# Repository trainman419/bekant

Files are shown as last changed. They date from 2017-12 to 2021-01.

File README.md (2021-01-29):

# IKEA Bekant Desk Controller

This is a simple Arduino firmware to control the IKEA Bekant motorized sit/stand desk.

## Circuit

The circuit for this sketch is based on an MCP2003B LIN transceiver.

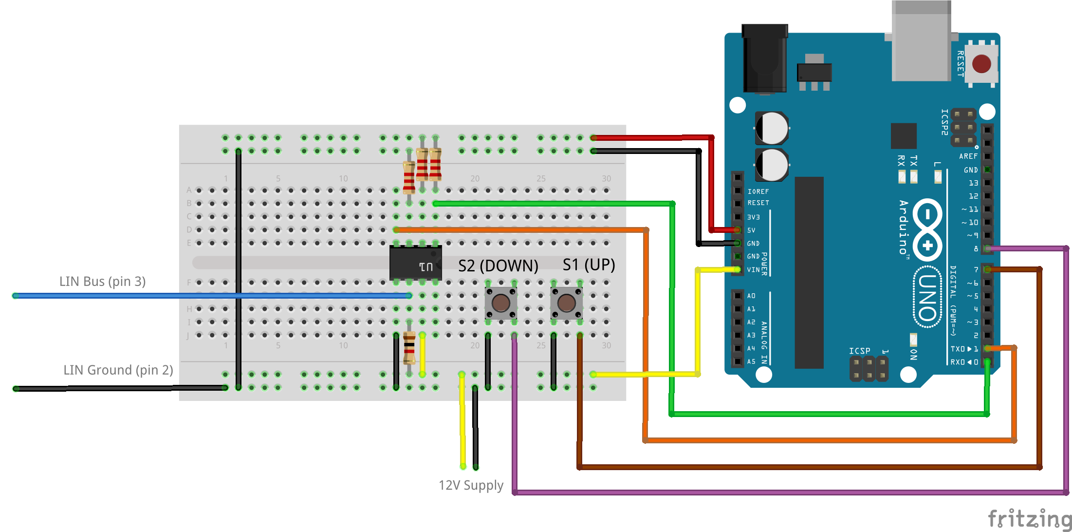
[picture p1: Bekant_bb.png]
Breadboard


And the accompanying schematic.

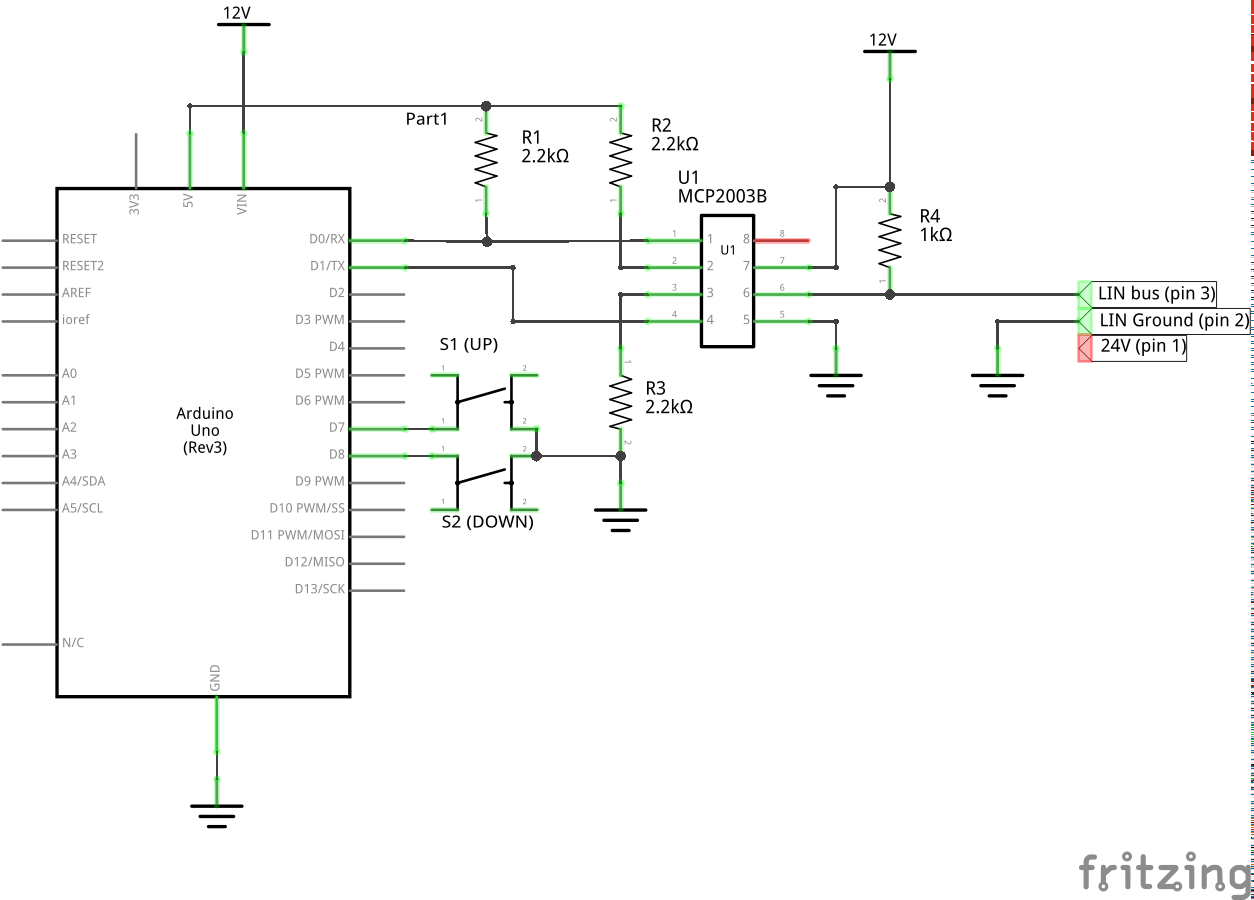
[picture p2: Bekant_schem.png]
Schematic


## Details of operation

Based on a blog post by Robert Nixdorf<sup>[1](#1)</sup>, it's quite clear that the desk is using the 1-wire LIN protocol<sup>[2](#2)</sup> to communicate between the controller and motors in both legs of the desk.

I've seen other posts from Gina Häußge<sup>[4](#4)</sup>, on the EEVblog forum <sup>[7](#7)</sup>, from Robin Reiter<sup>[6](#6)</sup>, and reposted on Hackaday<sup>[8](#8)</sup> and the AdaFruit Blog<sup>[9](#9)</sup>, but none of these have deciphered the LIN command protocol or completely replaced the existing controller. These hacks mostly focus reading the encoder value from LIN and sending button presses to the controller board, but modifications are a little messy, and I'd rather just plug into the bus and send commands directly.

LIN is a single-master bus, so in order to send commands we need to unplug the controller completely and replicate everything that it was doing in the replacement device. Luckily the protocol is simple, so this isn't too hard.

I am lucky enough to have access to an oscillocope that can do LIN decoding, so I used that extensively during my hacking and debugging.

The bus schedule was obvious by looking at the traffic. There is sequence of 10 messages, spaced 5 ms apart that repeat every 200ms. The ID sequence is 0x11, 0x08, 0x09, 0x10, 0x10, 0x10, 0x10, 0x10, 0x10, 0x01, 0x12.

I implemented a simple LIN master with an Arduino and a MCP2003B LIN transciever based on Andrew Stone's LIN library for arduino<sup>[5](#5)</sup> that can send these commands in the correct sequence, with the correct timing.

LIN is a single-wire shared bus, so it's impossible to tell which node is transmitting from a packet trace or oscilloscope readout. I know that the master must transmit the ID, so I set up my LIN master to transmit the IDs in sequence with no data. I saw that another device (presumably the motors) responded to IDs 0x08 and 0x09, so I know that the master should be reading from those IDs, and writing to the other IDs.

This means that the protocol is:

```
0x11: TX 0, 0, 0
0x08: RX 3 bytes
0x09: RX 3 bytes
0x10: TX 0 bytes; repeat 6 times
0x01: TX 0 bytes
0x12: TX 3 bytes
```

From my own decoding, and confirmed by the packet dumps in Robert Nixdorf's github repo<sup>[3](#3)</sup>, the pack format for 0x08, 0x09 and 0x12 seems to be a two-byte encoder value followed by a status or command byte. The first byte of the encoder value increments more quickly when the table is moving, so this is probably the LSB.

I've only seen three status codes on ID's 0x08 and 0x09:
```
0x60 desk not moving
0x02 starting to move
0x03 moving
```

I've seen more commands in the 0x12 message. These seem to be sent in a specific sequence:
```
0xFC not moving
0xC4 sent immediately before moving
0x86 up
0x85 down
0x87 1st command before stopping
0x84 2nd command before stopping
```

There are several other command codes in Robert Nixdorf's packet dumps that I haven't decoded yet. It looks like they are probably related to movement of the desk near the upper and lower limits.

I don't competely understand how the encoder values are used yet. Here are my observations so far:
 * The encoder values are clearly encoder values; they increment and the upper byte increments or decrements when the lower byte rolls over.
 * Higher values correspond to higher desk positions.
 * The encoder value in 0x08 always seems to be higher than 0x09. Unclear if this is by design or coincidence.
 * The encoder value in 0x12 seems to be a copy of the value in 0x08 or 0x09 most of the time, but I have occasionally seen other values.

I _think_ the encoder value is a target encoder value for one or both legs, and the command byte somehow releases a brake in each leg and commands it to move.

Sending 0x87 for a prolonged period of time causes the encoder values in 0x08 and 0x09 to reach the same values. Maybe this is an absolute positioning command?

Sending the wrong encoder values with the 0x85 (down?) command causes the motors to move unevenly and the desk to tilt. Sending 0x86 followed by 0x87 eventually corrects this.

# References
 1. <a name="1">https://web.archive.org/web/20190116092248/https://blog.rnix.de/hacking-ikea-bekant/</a>
 2. <a name="2">https://en.wikipedia.org/wiki/Local_Interconnect_Network</a>
 3. <a name="3">https://github.com/diodenschein/TableMem</a>
 4. <a name="4">https://plus.google.com/u/1/+GinaH%C3%A4u%C3%9Fge/posts/3U5k1qKdLxH?pageId=none</a>
 5. <a name="5">https://github.com/gandrewstone/LIN</a>
 6. <a name="6">https://github.com/robin7331/IKEA-Hackant</a>
 7. <a name="7">https://www.eevblog.com/forum/beginners/ikea-bekant-desk-motorised-hack/</a>
 8. <a name="8">http://hackaday.com/2017/02/10/ikea-standing-desk-goes-dumb-to-smart-with-lin-bus/</a>
 9. <a name="9">https://blog.adafruit.com/2017/03/27/smarkant-ikea-bekant-adjustable-sitstand-table-controller-reverse-engineered-controlled-with-alexa/</a>

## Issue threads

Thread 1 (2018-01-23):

delay_until

brunisgirl, 2018-01-23:
Hi,

What does the delay_until do? And why did you use "5" as argument?

Thanks

trainman419, 2018-01-23:
```
unsigned long t = 0;

void delay_until(unsigned long ms) {
  unsigned long end = t + (1000 * ms);
  unsigned long d = end - micros();

  // crazy long delay; probably negative wrap-around
  // just return
  if ( d > 1000000 ) {
    t = micros();
    return;
  }

  if (d > 15000) {
    unsigned long d2 = (d-15000)/1000;
    delay(d2);
    d = end - micros();
  }
  delayMicroseconds(d);
  t = end;
}
```

`delay_until()` and the associated global `t` is used to wait the specified amount of time since the previous call to `delay_until()`. This allows me to run the same sequence of code on a schedule, even if individual function calls take a slightly different amount of time each time.

The argument to `delay_until` is the number of milliseconds to delay (since the previous call to delay_until)

For example, if I have a function `foo()` that takes 1-2 milliseconds to execute, if I my loop is:

```
void loop() {
    foo(); // 1-2 mS
    delay(5); // 5 mS
}
```

The total loop time will be between 6 and 7 milliseconds, instead of the desired 5 milliseconds. Since I cannot predict exactly how long foo() will take, I cannot just adjust the delay.

With delay_until(), this loop always takes 5 milliseconds:

```
void loop() {
    foo(); // 1-2 mS
    delay_until(5); // wait until 5mS have passed
}
```

This is particularly important for LIN because the protocol requires that the first set of messages be sent every 5 milliseconds (5mS * 10 messages = 50 mS), and the entire set of messages repeats every 200mS, so at the end of the loop I delay for the remaining 150mS: https://github.com/trainman419/bekant/blob/f3733f8a28a3442db584cdb14d0de5f904b2de64/bekant.ino#L264-L265

Again, the important thing to note here is that if I used a normal delay() between messages or at the end of the main loop, the amount of time that it takes to handle WiFi clients would increase the loop time, and the other LIN devices would probably time out.

brunisgirl, 2018-01-23:
Thanks. OK I understand. But you talk about the protocol asking for 5 ms.
Where in LIN specification you found it? Or it is only for this particular
case?

On Jan 23, 2018 8:57 PM, "Austin" <notifications@github.com> wrote:

unsigned long t = 0;

void delay_until(unsigned long ms) {
  unsigned long end = t + (1000 * ms);
  unsigned long d = end - micros();

  // crazy long delay; probably negative wrap-around
  // just return
  if ( d > 1000000 ) {
    t = micros();
    return;
  }

  if (d > 15000) {
    unsigned long d2 = (d-15000)/1000;
    delay(d2);
    d = end - micros();
  }
  delayMicroseconds(d);
  t = end;
}

delay_until() and the associated global t is used to wait the specified
amount of time since the previous call to delay_until(). This allows me to
run the same sequence of code on a schedule, even if individual function
calls take a slightly different amount of time each time.

The argument to delay_until is the number of milliseconds to delay (since
the previous call to delay_until)

For example, if I have a function foo() that takes 1-2 milliseconds to
execute, if I my loop is:

void loop() {
    foo(); // 1-2 mS
    delay(5); // 5 mS
}

The total loop time will be between 6 and 7 milliseconds, instead of the
desired 5 milliseconds. Since I cannot predict exactly how long foo() will
take, I cannot just adjust the delay.

With delay_until(), this loop always takes 5 milliseconds:

void loop() {
    foo(); // 1-2 mS
    delay_until(5); // wait until 5mS have passed
}

This is particularly important for LIN because the protocol requires that
the first set of messages be sent every 5 milliseconds (5mS * 10 messages =
50 mS), and the entire set of messages repeats every 200mS, so at the end
of the loop I delay for the remaining 150mS: https://github.com/
trainman419/bekant/blob/f3733f8a28a3442db584cdb14d0de5
f904b2de64/bekant.ino#L264-L265

Again, the important thing to note here is that if I used a normal delay()
between messages or at the end of the main loop, the amount of time that it
takes to handle WiFi clients would increase the loop time, and the other
LIN devices would probably time out.

—
You are receiving this because you authored the thread.
Reply to this email directly, view it on GitHub
<https://github.com/trainman419/bekant/issues/1#issuecomment-359911130>,
or mute
the thread
<https://github.com/notifications/unsubscribe-auth/AVm9d9d4HBNh6KV0pDWPqdkhFE5n1UpLks5tNjmtgaJpZM4RpxEQ>
.

trainman419, 2018-01-23:
The 5mS and 200mS loop rates are for this specific application. I measured these timings with my oscilloscope when I was reverse-engineering the protocol for the desk.

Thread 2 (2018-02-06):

Won't Activate - New Firmware?

joeljacobs, 2018-02-06:
I have followed your example and schematic as perfectly as possible. Quntuple-checking every connection, but the desk never moves. I have switched back and forth to the built-in controller, and it always works, but the Arduino never does. Is it possible the firmware changed on the desk?
I am also using an MCP2003 (not 2003B.) It doesn't seem like that should make a difference, but could it? The B supports LIN 2.2, and the one I have supports up to 2.1, but I can't imagine that's an issue.
Any hints? I can't troubleshoot it the way I understand, because the serial port is in use for the LIN chip.
I tried switching (using an arduino mega) to other serial pins using the constants, but it always outputted on the usb serial when connected.
I also ensure the usb serial is disconnected before testing.
Any advice would be great.

trainman419, 2018-02-06:
If you have one, your best bet would be to hook up an oscilloscope on the LIN bus and see that there's traffic (it should look similar to normal RS-232 traffic).

Trying an Arduino Mega is also an excellent debugging idea; but in addition to changing the pins ( https://github.com/trainman419/bekant/blob/master/bekant.ino#L22-L23 ) you'll also need to change the serial port used by the LIN library: https://github.com/trainman419/bekant/blob/master/bekant.ino#L26

gcormier, 2018-03-04:
Solved the issue. @joeljacobs not sure if you are still working on this.

The schematic here is missing two key diodes. (The MCP2003B reference diagram is also wrong). The official LIN spec is where I figured it out.

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

You MUST have these two diodes in serial tapped in this manner to provide the proper voltage drop.

I think otherwise, the behaviour is erratic - we can assume @trainman419 had a fully functional setup without them. I had a half functional setup, with one motor responding and the other not. Probably depends on if other parts of the circuit induce some voltage drop.

trainman419, 2018-03-04:
I never saw any signal integrity issues without the diodes that you're mentioning, and I don't remember seeing them in the LIN bus specification. Can you provide a link to documentation about these diodes, or measurements that demonstrate why they're necessary?

I do know that there is some setup that is performed by the desk's original controller that I haven't emulated yet, and I remember trying to power my desk on without the original controller would result in only a single working motor.

Usually I power on the desk with the original controller, then unplug it and plug in my Arduino.

gcormier, 2018-03-05:
Interesting on the setup - I will have to try it out.

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

Two pages down it says the diodes are mandatory.

gcormier, 2018-03-05:
Damn, I just tried it out - indeed, does not work without initially having the IKEA controller plugged in first. Sigh. Time to figure out the initialization routine!

jeffreypriebe, 2018-04-14:
@gcormier Any luck on figuring out the initialization routine?

I presume "power desk on" is referring to plugging in the desk. That is, the following should work:
1. Plug in desk (with normal desk controller)
2. Disconnect the controller
3. Attach this controller

However, reversing steps 2 & 1 will make it fail.

gcormier, 2018-04-14:
Yes I got it going. I started a project with memory functions, PCB and functional controller.

https://github.com/gcormier/megadesk

gcormier, 2018-04-14:
Oh and looking back at this issue, the diodes might not have been the root cause as I was unaware of the initialization routine. However still good to include them.

luckydonald, 2019-12-30:
Is that starting sequence now brought back into this arduino project or only available at megadesk one?

If I read @gcormier's code correctly, that's the part of https://github.com/gcormier/megadesk/blob/39d9ab13acb1d6baa30617af4301626e288f1aac/Code/megadesk.ino#L472-L565, yes?

trainman419, 2019-12-30:
I haven't ported @gcormier 's changes back to this repository. I'd be happy to accept a pull request if someone else wants to do it.

slaesh, 2020-02-07:
i am currently working on a complete replacement..
including a display, wifi and a custom enclosure! :)
just remove the old controller, replace with the new one and keep on going! ;)

will keep you guys updated =)

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

rhannink, 2021-05-05:
Hello,
I have built a LIN controller as shown in the schematic. I only use an mcp2003 e/p instead off an MCP2003B.
I have the Bekant desk plugged in with the original controller, next I remove the original controller an plug in the Arduino controller still with the Bekant desk powered on.

The desk does not respons to and button press. I see the Arduino Led lightning up when I press a button. I have also connected a logic analyser to the RX and TX pin (0 and 1) and I see LIN protocols going by. I think I even see LIN respons to ID 0x08 and LIN respons to ID 0x09.

And idea what i might be doing wrong or how I can do further debugging?

Gr. Remco
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

trainman419, 2021-05-05:
As noted before, there's an initialization sequence for the motors that I haven't reverse-engineered or implemented, but it looks like @gcormier has. I suggest you copy that init code over into this project and give it a try: https://github.com/gcormier/megadesk/blob/39d9ab13acb1d6baa30617af4301626e288f1aac/Code/megadesk.ino#L472-L565

rhannink, 2021-05-05:
Thank for your response, but I read everywhere that starting up with the original controller and then switch to the new controller should do the trick.

I am not a (real) programmer so adding the startup code is not trivial for me, but I will give it a try.

trainman419, 2021-05-05:
You write code? That makes you a programmer.

I'll tell you a little secret. I have a very fancy title at my day job and I still look things up on google and stack overflow all the time.

I tried my controller with a new desk, maybe a year or two ago, and ran into the same problem here. Couldn't get it to sync and didn't have the tools to look into it at the time.

I don't have one of these desks handy at the moment so you're probably in a better position to fix it than I am. It looks like you've got a nice logic analyzer there. I'd probably start by trying to copy or modify @gcormier's code into the arduino setup() function here. If that doesn't help, you could use your logic analyzer to capture the power-on command sequence from the original controller and modify the code here until it produces the same power-up sequence.

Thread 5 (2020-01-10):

Get MCP2003B to work with 3.3V ESP8266?

left4taco, 2020-01-10:
@trainman419 You did a very good job! I was using two relay to simulate the button but that's just an ugly solution. It's way better to communicate to the LIN bus directly.

Btw, I'm using ESP8266 in my project. The only problem is that it's output pin has a voltage of 3.3V instead of 5V on an Arduino. I checked the datasheet of [MCP2003B](http://ww1.microchip.com/downloads/en/DeviceDoc/2000546C3.pdf) and found these about the TDX and RDX:

> RDX: It has to be at a high level (> 2.5V typical) while LBUS is recessive

Looks like 3.3V from ESP8266 pin is just fine.

> TDX: has an internal pull-up

I don't if the voltage here will be 5V or 12V, but both are higher than the max tolerant voltage of ESP8266 pin.

Do you have any thought about this problem? I mean I can use a MOSFET as a gate but that seems to be an overkill.

Thanks!

zoltanhosszu, 2020-05-18:
@left4taco were you able to solve this? I'm in the exact same situation with a NodeMCU

nschurando, 2021-01-27:
Interested as well.

trainman419, 2021-01-29:
I have an MCP2003B hooked up to a [Sparkfun Thing Dev (ESP8266)](https://www.sparkfun.com/products/13711) and I have not had trouble with it.

I seem to remember finding something about this in the MCP2003B data sheet, but I don't remember exactly where.

satrik, 2021-02-22:
@trainman419 I'm also struggling with my esp8266 (Wemos D1 Mini).

To make the debugging easier, I've switched the lin.h to SoftwareSerial and use the USB port (HardwareSerial) to get some console output. I get a proper answer for the current height (enc_a).
```
12:58:30.436 -> enc_a
12:58:30.436 -> 1503
```
I'm wondering about the output of `node_a[2]` and `node_b[2]` between the 2 `switch(state)` in the loop. Neither a button is pressed or not, it shows always:
```
12:58:30.647 -> node_a[2]
12:58:30.647 -> 37
12:58:30.647 -> node_b[2]
12:58:30.647 -> 37
```

Do you have any idea what the `37` means and what I could check/test next?

Btw. I've the bigger size bekant and according to the megadesk repo, I've changed this line `if (node_a[2] == 0x00 && node_b[2] == 0x00)`. I've also tried it with 0x60, but it does not change anything so far.

b1sp, 2021-02-22:
while reading my own comment, I think I should try this `if (node_a[2] == 0x25 && node_b[2] == 0x25)`. maybe my table reports it's idle neither as 0x00 nor as 0x60 🤔

satrik, 2021-02-22:
while reading my own answer, I think I should try `if (node_a[2] == 0x25 && node_b[2] == 0x25)` 🤔
maybe my table reports it's idle as 37 and not as 96 or 0.

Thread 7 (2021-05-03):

Compiling error for esp8266

rhannink, 2021-05-03:
Hallo,

Great project, I'd like to automate my bekent desk with your project. Compiling the code for an Arduino Uno works fine, but compiling it for esp8266 with the webserver results in:

```/Users/remco/Code/Arduino/bekant/bekant.ino: In function 'int restCallback(String)':
bekant:68:15: error: 'class aREST_UI' has no member named 'buttonCallback'
   return rest.buttonCallback(answer);
               ^
/Users/remco/Code/Arduino/bekant/bekant.ino: In function 'void setup()':
bekant:87:8: error: 'class aREST_UI' has no member named 'buttonFunction'
   rest.buttonFunction("Up", &up);
        ^
bekant:88:8: error: 'class aREST_UI' has no member named 'buttonFunction'
   rest.buttonFunction("Down", &down);
        ^
exit status 1
'class aREST_UI' has no member named 'buttonCallback'
```

I have aRest library version 2.9.1 and aREST_UI library version 1.1.1 installed.

And idea what i might do wrong?

Gr. Remco

trainman419, 2021-05-04:
Huh. I don't remember which version of aREST_UI I used for this and I can't find anything about the buttonCalback or buttonFunction in their public docs or git history.

The web UI never worked terribly well to begin with; I mostly built it to prank the other people who shared my office at work. It might be better to scrap most of the web server code and start over.

I'll keep an eye out for the original source code for those libraries and let you know if I find them.

Also take a look at the megadesk project: https://github.com/gcormier/megadesk . I think he has a more complete implementation of the LIN commands and startup sequence for this desk.

trainman419, 2021-05-04:
Ah; here we are. I completely forgot that I have modified versions of the aREST_UI and aREST libraries that I was using for this project: https://github.com/trainman419/aREST_UI and https://github.com/trainman419/aREST ( I merged my changes to aREST so you just need aREST_UI )

rhannink, 2021-05-05:
Ok thanks,

I already looked at the code of megadesk, but this is strictly for tinyAT and i am not sure if it will compile on esp8266 or esp32. My goal is to het it up and running with an ESP with MQTT so I can control it from Home Assistant and Google.

Thanks for you work, I will keep you informed on my progression.

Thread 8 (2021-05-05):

New controller not doing anything

rhannink, 2021-05-05:
Hello,
I have built a LIN controller as shown in the schematic. I only use an mcp2003 e/p instead off an MCP2003B.
I have the Bekant desk plugged in with the original controller, next I remove the original controller an plug in the Arduino controller still with the Bekant desk powered on.

The desk does not respons to and button press. I see the Arduino Led lightning up when I press a button. I have also connected a logic analyser to the RX and TX pin (0 and 1) and I see LIN protocols going by. I think I even see LIN respons to ID 0x08 and LIN respons to ID 0x09.

And idea what i might be doing wrong or how I can do further debugging?

Gr. Remco

`
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

`

trainman419, 2021-05-05:
See #2 .

Closed 2021-05-05.

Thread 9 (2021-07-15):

Can my desk use 3 legs?

petersenna, 2021-07-15:
Hi I am looking into upgrading my desk, but I need 3 legs. I am considering buying 4 legs, but use only 3 of them. Problem is I could not find out if the protocol work with only one master and two slaves, or if I can have 3 slaves as well? Thank you!

petersenna, 2021-07-15:
Err I guess I got my answer on wikipedia: `LIN is a broadcast serial network comprising 16 nodes (one master and typically up to 15 slaves)`.

So I guess it is likely to work with up to 15 legs :smile:

trainman419, 2021-07-16:
I would be cautious here. I think LIN assumes that each device has a unique address and I think the Bekant legs have some protocol extension to assign unique addresses to each leg on startup. I'm not sure if that protocol extends to assigning unique address for more than two legs.

Even if the legs support it, you will probably need to spend some time porting over the initialization code ( see #2 ) and then understand it well enough to try to extend it to 3 legs.

gritstub, 2022-08-31:
@petersenna : Did you ever solve this issue? I am trying to set up a Bekant with 3 or 4 legs.

petersenna, 2022-08-31:
> @petersenna : Did you ever solve this issue? I am trying to set up a Bekant with 3 or 4 legs.

@gritstub I went on a different direction. I kept my static table.

To stand, I use monitor arm that has enough range for sitting and standing, and I use an Medical Adjustable Overbed Bedside Table for the wireless keyboard and mouse.

Notice the long pole: https://www.digitec.ch/en/s1/product/ergotron-table-mounting-arm-table-46-monitor-mount-4656121

https://www.amazon.ca/Medical-Adjustable-Overbed-Bedside-Hospital/dp/B00QMNTMXA

Closed 2022-08-31.

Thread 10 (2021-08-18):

Where to get MCP2003B? 🤔

M4RKU5-C0D3, 2021-08-18:
Hi,

I was wondering where you got the MCP2003B from? I'd prefer a DIP8 but can't find any 🙈

Greetings
Markus

trainman419, 2021-08-18:
It looks like Microchip only makes the MCP2003B in surface-mount packages.

For my prototyping I used the MCP2003B in the SOIC-8 package, on one of Adafruit's SOIC-8 breakout boards: https://www.adafruit.com/product/1212 .

The MCP2003-E/P is an older chip but it's available in a DIP package: https://octopart.com/mcp2003-e%2Fp-microchip-18190209?r=sp . I haven't tested it, but it may work in a similar way. Depending on which variant you choose, you may need to hook up some of the secondary signals differently.

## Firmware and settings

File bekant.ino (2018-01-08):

#include "lin.h"

#ifdef ESP8266
#include <ESP8266WiFi.h>
#include <aREST.h>
#include <aREST_UI.h>

// Pin settings for Sparkfun ESP8266 Thing Dev
#define UP_BTN 0
#define DOWN_BTN 13
#define LED 5
#define LED_ON LOW
#define TX_PIN 1
#define RX_PIN 3

#else
// Standard arduino settings
#define UP_BTN 7
#define DOWN_BTN 8
#define LED 13
#define LED_ON HIGH
#define TX_PIN 1
#define RX_PIN 0
#endif

Lin lin(Serial, TX_PIN);

#ifdef ESP8266
aREST_UI rest = aREST_UI();

const char * ssid = "Linksays";

WiFiServer server(80);
#endif

int height = 0;

enum class Command {
  NONE,
  UP,
  DOWN,
};

Command user_cmd = Command::NONE;

int up(bool pushed) {
  if(pushed) {
    digitalWrite(LED, LED_ON);
    user_cmd = Command::UP;
  } else {
    digitalWrite(LED, !LED_ON);
    user_cmd = Command::NONE;
  }
}

int down(bool pushed) {
  if(pushed) {
    digitalWrite(LED, LED_ON);
    user_cmd = Command::DOWN;
  } else {
    digitalWrite(LED, !LED_ON);
    user_cmd = Command::NONE;
  }
}

#ifdef ESP8266
int restCallback(String answer) {
  return rest.buttonCallback(answer);
}
#endif

void setup() {
  // put your setup code here, to run once:
  lin.begin(19200);

  pinMode(UP_BTN, INPUT_PULLUP);
  pinMode(DOWN_BTN, INPUT_PULLUP);
  pinMode(LED, OUTPUT);
  digitalWrite(LED, !LED_ON);

#ifdef ESP8266
  rest.title("Desk");
  rest.variable("Height", &height);
  rest.label("Height");
  rest.set_name("esp8266");

  rest.buttonFunction("Up", &up);
  rest.buttonFunction("Down", &down);
  rest.function("ui_callback", &restCallback);

  WiFi.mode(WIFI_AP);

  //WiFi.softAP(ssid, password);
  WiFi.softAP(ssid);

  server.begin();
#endif
}

unsigned long t = 0;

void delay_until(unsigned long ms) {
  unsigned long end = t + (1000 * ms);
  unsigned long d = end - micros();

  // crazy long delay; probably negative wrap-around
  // just return
  if ( d > 1000000 ) {
    t = micros();
    return;
  }
  
  if (d > 15000) {
    unsigned long d2 = (d-15000)/1000;
    delay(d2);
    d = end - micros();
  }
  delayMicroseconds(d);
  t = end;
}

enum class State {
  OFF,
  STARTING,
  UP,
  DOWN,
  STOPPING1,
  STOPPING2,
};

State state = State::OFF;

void loop() {
  // put your main code here, to run repeatedly:
  uint8_t empty[] = { 0, 0, 0 };
  uint8_t node_a[4] = { 0, 0, 0, 0 };
  uint8_t node_b[4] = { 0, 0, 0, 0 };
  uint8_t cmd[3] = { 0, 0, 0 };
  uint8_t res = 0;


  // Send ID 11
  lin.send(0x11, empty, 3, 2);
  delay_until(5);

  // Recv from ID 08
  res = lin.recv(0x08, node_a, 3, 2);
  delay_until(5);

  // Recv from ID 09
  res = lin.recv(0x09, node_b, 3, 2);
  delay_until(5);

  // Send ID 10, 6 times
  for (uint8_t i = 0; i < 6; i++) {
    lin.send(0x10, 0, 0, 2);
    delay_until(5);
  }

  // Send ID 1
  lin.send(0x01, 0, 0, 2);
  delay_until(5);

  uint16_t enc_a = node_a[0] | (node_a[1] << 8);
  uint16_t enc_b = node_b[0] | (node_b[1] << 8);
  uint16_t enc_target = enc_a;
  height = enc_a;

  // Send ID 12
  switch (state) {
    case State::OFF:
      cmd[2] = 0xFC; // 0b11111100
      break;
    case State::STARTING:
      cmd[2] = 0xC4; // 0b10100100
      break;
    case State::UP:
      enc_target = min(enc_a, enc_b);
      cmd[2] = 0x86; // 0b10000110
      break;
    case State::DOWN:
      enc_target = max(enc_a, enc_b);
      cmd[2] = 0x85; // 0b10000101
      break;
    case State::STOPPING1:
      cmd[2] = 0x87; // 0b10000111
      break;
    case State::STOPPING2:
      cmd[2] = 0x84; // 0b10000100
      break;
  }
  cmd[0] = enc_target & 0xFF;
  cmd[1] = enc_target >> 8;
  lin.send(0x12, cmd, 3, 2);

  // read buttons and compute next state
#ifndef ESP8266
  if (digitalRead(UP_BTN) == 0) { // UP
    up(true);
  } else if (digitalRead(DOWN_BTN) == 0) { // DOWN
    down(true);
  } else {
    up(false);
  }
#endif

  switch (state) {
    case State::OFF:
      if (user_cmd != Command::NONE) {
        if ( node_a[2] == 0x60 && node_b[2] == 0x60) {
          state = State::STARTING;
        }
      }
      break;
    case State::STARTING:
      //if( node_a[2] == 0x02 && node_b[2] == 0x02) {
        switch(user_cmd) {
          case Command::NONE:
            state = State::OFF;
            break;
          case Command::UP:
            state = State::UP;
            break;
          case Command::DOWN:
            state = State::DOWN;
            break;
        }
      //}
      break;
    case State::UP:
      if (user_cmd != Command::UP) {
        state = State::STOPPING1;
      }
      break;
    case State::DOWN:
      if (user_cmd != Command::DOWN) {
        state = State::STOPPING1;
      }
      break;
    case State::STOPPING1:
      state = State::STOPPING2;
      break;
    case State::STOPPING2:
      if ( node_a[2] == 0x60 && node_b[2] == 0x60) {
        state = State::OFF;
      }
      break;
    default:
      state = State::OFF;
      break;
  }

#ifdef ESP8266
  // Use the remaining time to service clients
  WiFiClient client = server.available();
  if(client) {
    while(!client.available()) {
      delay(1);
    }
    rest.handle(client);
  }
#endif

  // Wait the remaining 150 ms in the cycle
  delay_until(150);
}

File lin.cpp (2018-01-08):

/*
 Copyright 2011 G. Andrew Stone
All rights reserved.

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
THIS SOFTWARE IS PROVIDED BY THE COPYRIGHT HOLDERS AND CONTRIBUTORS "AS IS" AND
ANY EXPRESS OR IMPLIED WARRANTIES, INCLUDING, BUT NOT LIMITED TO, THE IMPLIED
WARRANTIES OF MERCHANTABILITY AND FITNESS FOR A PARTICULAR PURPOSE ARE
DISCLAIMED. IN NO EVENT SHALL <COPYRIGHT HOLDER> BE LIABLE FOR ANY
DIRECT, INDIRECT, INCIDENTAL, SPECIAL, EXEMPLARY, OR CONSEQUENTIAL DAMAGES
(INCLUDING, BUT NOT LIMITED TO, PROCUREMENT OF SUBSTITUTE GOODS OR SERVICES;
LOSS OF USE, DATA, OR PROFITS; OR BUSINESS INTERRUPTION) HOWEVER CAUSED AND
ON ANY THEORY OF LIABILITY, WHETHER IN CONTRACT, STRICT LIABILITY, OR TORT
(INCLUDING NEGLIGENCE OR OTHERWISE) ARISING IN ANY WAY OUT OF THE USE OF THIS
SOFTWARE, EVEN IF ADVISED OF THE POSSIBILITY OF SUCH DAMAGE.
*/

#include "Arduino.h"
#include "lin.h"

Lin::Lin(LIN_SERIAL& ser,uint8_t TxPin)
  : serial(ser)
  , txPin(TxPin)
{
}

void Lin::begin(int speed)
{
  serialSpd = speed;
  serial.begin(serialSpd);
  serialOn  = 1;

  unsigned long int Tbit = 100000/serialSpd;  // Not quite in uSec, I'm saving an extra 10 to change a 1.4 (40%) to 14 below...
  unsigned long int nominalFrameTime = ((34*Tbit)+90*Tbit);  // 90 = 10*max # payload bytes + checksum (9). 
  timeout = LIN_TIMEOUT_IN_FRAMES * 14 * nominalFrameTime;  // 14 is the specced addtl 40% space above normal*10 -- the extra 10 is just pulled out of the 1000000 needed to convert to uSec (so that there are no decimal #s).
}

// Generate a BREAK signal (a low signal for longer than a byte) across the serial line
void Lin::serialBreak(void)
{
  if (serialOn) {
    serial.flush();
    serial.end();
  }

  pinMode(txPin, OUTPUT);
  digitalWrite(txPin, LOW);  // Send BREAK
  const unsigned long int brkend = (1000000UL/((unsigned long int)serialSpd));
  const unsigned long int brkbegin = brkend*LIN_BREAK_DURATION;
  if (brkbegin > 16383) delay(brkbegin/1000);  // delayMicroseconds unreliable above 16383 see arduino man pages
  else delayMicroseconds(brkbegin);
  
  digitalWrite(txPin, HIGH);  // BREAK delimiter

  if (brkend > 16383) delay(brkend/1000);  // delayMicroseconds unreliable above 16383 see arduino man pages
  else delayMicroseconds(brkend);

  serial.begin(serialSpd);
  serialOn = 1;
}

/* Lin defines its checksum as an inverted 8 bit sum with carry */
uint8_t Lin::dataChecksum(const uint8_t* message, char nBytes,uint16_t sum)
{
    while (nBytes-- > 0) sum += *(message++);
    // Add the carry
    while(sum>>8)  // In case adding the carry causes another carry
      sum = (sum&255)+(sum>>8); 
    return (~sum);
}

/* Create the Lin ID parity */
#define BIT(data,shift) ((addr&(1<<shift))>>shift)
uint8_t Lin::addrParity(uint8_t addr)
{
  uint8_t p0 = BIT(addr,0) ^ BIT(addr,1) ^ BIT(addr,2) ^ BIT(addr,4);
  uint8_t p1 = ~(BIT(addr,1) ^ BIT(addr,3) ^ BIT(addr,4) ^ BIT(addr,5));
  return (p0 | (p1<<1))<<6;
}

/* Send a message across the Lin bus */
void Lin::send(uint8_t addr, const uint8_t* message, uint8_t nBytes,uint8_t proto)
{
  uint8_t addrbyte = (addr&0x3f) | addrParity(addr);
  uint8_t cksum = dataChecksum(message,nBytes,(proto==1) ? 0:addrbyte);
  serialBreak();       // Generate the low signal that exceeds 1 char.
  serial.write(0x55);  // Sync byte
  serial.write(addrbyte);  // ID byte
  serial.write(message,nBytes);  // data bytes
  serial.write(cksum);  // checksum
  serial.flush();
}

uint8_t Lin::recv(uint8_t addr, uint8_t* message, uint8_t nBytes,uint8_t proto)
{
  uint8_t bytesRcvd=0;
  unsigned int timeoutCount=0;
  serialBreak();       // Generate the low signal that exceeds 1 char.
  serial.flush();
  serial.write(0x55);  // Sync byte
  uint8_t idByte = (addr&0x3f) | addrParity(addr);
  serial.write(idByte);  // ID byte
  bytesRcvd = 0xfd;
  do { // I hear myself
    while(!serial.available()) { delayMicroseconds(100); timeoutCount+= 100; if (timeoutCount>=timeout) goto done; }
  } while(serial.read() != 0x55);
  bytesRcvd = 0xfe;
  do {
    while(!serial.available()) { delayMicroseconds(100); timeoutCount+= 100; if (timeoutCount>=timeout) goto done; }
  } while(serial.read() != idByte);


  bytesRcvd = 0;
  for (uint8_t i=0;i<nBytes;i++)
  {
    // This while loop strategy does not take into account the added time for the logic.  So the actual timeout will be slightly longer then written here.
    while(!serial.available()) { delayMicroseconds(100); timeoutCount+= 100; if (timeoutCount>=timeout) goto done; } 
    message[i] = serial.read();
    bytesRcvd++;
  }
  while(!serial.available()) { delayMicroseconds(100); timeoutCount+= 100; if (timeoutCount>=timeout) goto done; }
  if (serial.available())
  {
    uint8_t cksum = serial.read();
    bytesRcvd++;
    if (proto==1) idByte = 0;  // Don't cksum the ID byte in LIN 1.x
    if (dataChecksum(message,nBytes,idByte) == cksum) bytesRcvd = 0xff;
  }

done:
  serial.flush();

  return bytesRcvd;
}

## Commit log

2017-08-25 LIN control of desk from Arduino
2017-12-18 Add Fritzing schematic and breadboard example
    [Bekant.fzz]
2017-12-18 Update README with schematic
2017-12-18 Rename to make arduino happy
2017-12-18 Update schematic with up/down buttons
    [Bekant.fzz]
2017-12-19 Update with pin numbers
    [Bekant.fzz]
2018-01-08 Fix remaining pin issues
    [bekant.ino, lin.cpp]
2018-01-08 Restore Arduino Uno compatibility
2018-01-08 Fixed command codes. Working!
    [bekant.ino]
